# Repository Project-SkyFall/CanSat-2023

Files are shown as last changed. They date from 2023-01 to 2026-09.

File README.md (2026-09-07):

# Disclaimer
This README isn't finished and will be edited in near future

# CanSat-2023
This is a repository of the Czech CanSat team Project SkyFall, winner of CanSat's 2023 Czech national round

<div align="center">
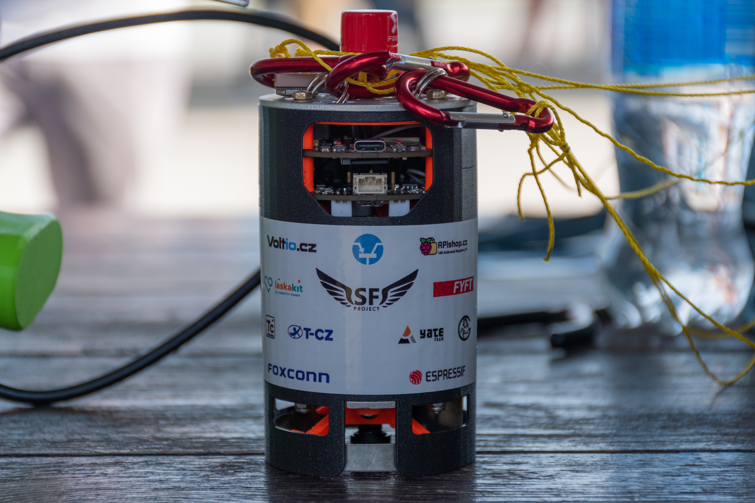
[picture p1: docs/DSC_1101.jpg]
CanSat 2023
  
</div>

## Documentation

<!-- About team -->

## About the team

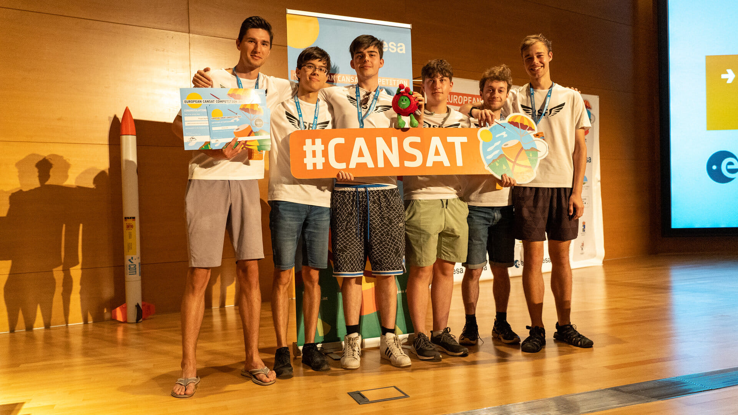
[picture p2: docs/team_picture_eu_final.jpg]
  

  ### Vít Brázda
  <table><tr>
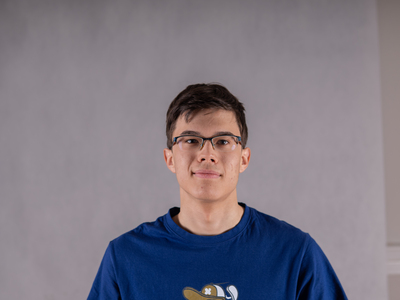
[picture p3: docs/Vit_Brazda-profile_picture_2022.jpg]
    <td width="250"></td>
    <td>Vít is responsible for data visualization running on ground station, as well as making index of habitability of planet, where CanSat is landing. He has a lot of experience regarding Python.</td>
  </tr></table>

  ### David Haisman
  <table><tr>
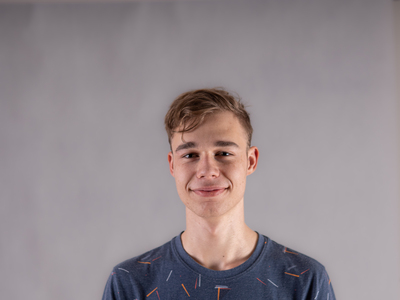
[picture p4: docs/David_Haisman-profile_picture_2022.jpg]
David Haisman
    <td width="250"></td>
    <td>David handles electronics and programming on our CanSat. He designed PCB's, made some libraries and wrote the whole CanSat code. During the development of the CanSat he gained a lot of experience regarding PCB design and programming in C++.</td>
  </tr></table>

  ### Radim Leština
  <table><tr>
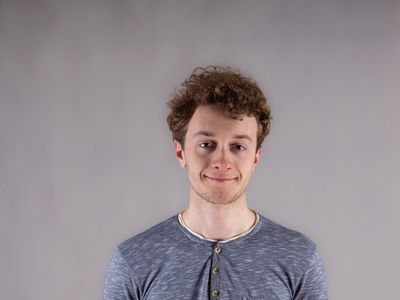
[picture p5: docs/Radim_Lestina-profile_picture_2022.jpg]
Radim Leština
    <td width="250"></td>
    <td>Radim is in charge of designing the outer construction of the CanSat itself. He has a lot of experience in designing and 3D printing mechanical contraptions.</td>
  </tr></table>

  ### Václav Horáček
  <table><tr>
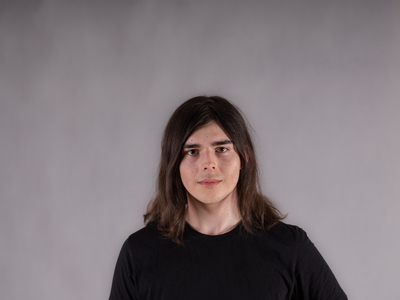
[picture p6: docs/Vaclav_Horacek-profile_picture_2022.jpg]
Václav Horáček
    <td width="250"></td>
    <td>Václav is in charge of multiple departments, mainly the ones for documentation and recovery. In documentation he made the styles, graphics and oversees the documentation making process. His contribution in the recovery department is designing and sewing the CanSat's parachute.</td>
  </tr></table>

  ### Lukáš Nastoupil
  <table><tr>
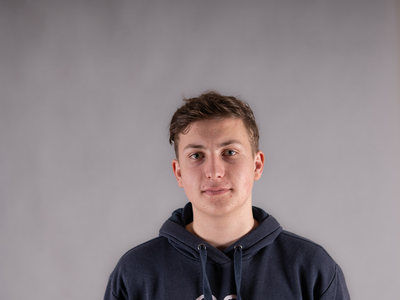
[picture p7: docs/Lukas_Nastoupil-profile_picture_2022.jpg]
Lukáš Nastoupil
    <td width="250"></td>
    <td>Lukáš designed and made the ground station, which is an essential part for our secondary mission. He designed the PCB's, modeled and programmed the ground station. He also worked on the real-time transmission of video from CanSat down to the ground station.</td>
  </tr></table>

  ### Adam Keřka
  <table><tr>
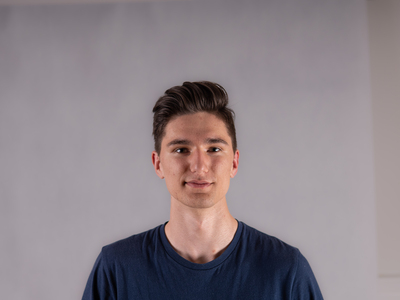
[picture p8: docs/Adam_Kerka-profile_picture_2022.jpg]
Adam Keřka
    <td width="250"></td>
    <td>Adam leads the team itself and also the department of publicity. This mainly includes maintaining social networks accounts and communicating with sponsors. He also designed a lot of the graphics used in advertising and posts on social networks.</td>
  </tr></table>

  ### Vladimír Kašpar
  Ing. Vladimír Kašpar is our mentor in the CanSat competition. We chose Vladimír Kašpar as our mentor based on his experience. In the CanSat 2019 he was a mentor of team Charles the fourth that made it to the European finale. He is also an electronics teacher at SPŠE a VOŠ Pardubice.

  ### Jan Novotný
  Jan Novotný is a freelance developer who makes web and mobile applications. He programmed the Project SkyFall webpage and supports our team on various other competitions and outgoings.

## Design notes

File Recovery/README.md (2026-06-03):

# Recovery

Mission is rather simple: To protect the satellite from hitting the ground at very high speed. <br>
While a primitive solution, a parachute is good enough. <br>
With some calculations, one can determine exact falling speed of the satellite. <br>
<br>
This branch is dedicated to research and realisation of said recovery systems. <br>

## Let's do this...

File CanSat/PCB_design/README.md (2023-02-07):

# PCB design
## Content
* ### [Disclaimer](#disclaimer-1)
* ### [Power Unit](#power-unit-1)

## Disclaimer
PCBs designed in KiCad

## Power Unit
### Description
Power Unit is base PCB from stackup. It charges batteries or supplies rest of CanSat with 5 V power.
### Used ICs
#### MP2639A
* Balances 2s Li-po batteries and charges them from USB
* Overvoltage, overcurrent and overtemperature battery protection
* Step-down battery voltage to 5 V

## Control Unit
### Description

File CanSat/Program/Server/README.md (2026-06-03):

# Pokyny pro ovládání senzorů

- Funkce get_sensors po dotazu na /sensors očekává odpověď ve formátu
```json
[
    {
        "sensor": "<sensor_name>",
        "value": "<sensor_value>"
    }
]
```
Senzory, které chceme pouze zapnout a vypnout, musí mít nastavenou hodnotu `sensor_value` na "on", nebo "off"

- Po volbě stavu senzoru je odeslán dotaz na / s parametry ve tvaru
```json
{
    "sensor": "<sensor_name>",
    "value": "<sensor_value>"
}
```

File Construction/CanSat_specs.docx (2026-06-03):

CanSat

Rozměry

- 115 mm (výška)
- 66 mm (průměr)

Vše musí být uvnitř, vyjma padáku, ten může přidávat velikost pouze směrem nahoru, ne do strany! (stejně jako externí antény), pro externí prvky je nad CanSatem rezervováno 4,5 cm místa.

Váha

300-350 g

Baterie

- Baterie musí být vyjímatelná
- CanSat musí v zapnutém stavu vydržet na baterii minimálně 4 hod. (čistého času)

Padák

- Musí vydržet tažnou sílu 1000 N
- Doporučená přistávací rychlost je 6 m×s⁻¹, nebo míň
- CanSat jako takový musí zvládnout zrychlení 20 g

Budget

Musíme se vejít do 12 729,07 Kč (XD)

Kvalita vzduchu

6,3 x 6,2 x 0,2 cm

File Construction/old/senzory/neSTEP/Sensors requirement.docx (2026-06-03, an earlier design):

Sensor requirements EN

SCD30

- CO2, Humidity, temperature
- Requires acces to „fresh“ air
- Must be out of main air flow and any hot source

SEN0322

- Oxygen
- must not be subject to excessive impact or vibration

BME280

- Humidity
- Just needs „fresh“ air

SD CARD READER

- Data transfer
- Requires easy acces

BATTERIES

- Power supply
- Must be possible to replace it

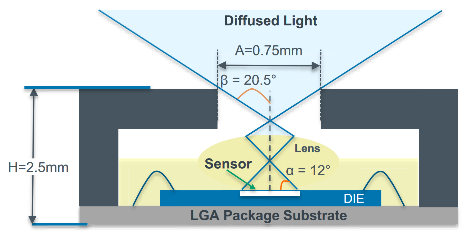
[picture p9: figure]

AS7265X

- Spektrometre
- Needs acces to a ambient light

BH1750

- Light intrnsity
- Needs acces to a ambient light

MPU9250

- Gyroscope, Accelerometer, Magnetometer

Požadavky sensorů CZ

SCD30

- CO2, vlhkost, teplota
- Potřebuje přístup k okolnímu vzduchu
- Musí být mimo hlavní tok vzduchu a jakémukoliv zdroji významného tepla

SEN0322

- Vzduch
- Neměl by být vystaven vibracím, nebo prudkým nárazům (r.i.p.)

BME280

- Vlhkost
- Přístup k okolnímu vzduchu

ČTEČKA SD KARTY

- Přenos dat
- Potřebuje snadný přístup

BATERIE

- Zdroj
- Musí být možné je vyměnit

AS7265X

- Spektrometr
- Potřebuje přístup k okolnímu světlu

BH1750

- Light intrnsity
- Potřebuje přístup k okolnímu světlu

BH1750

- Gyroskop, Akcelerometr, Magnetometr
- Needs acces to a ambient light 8

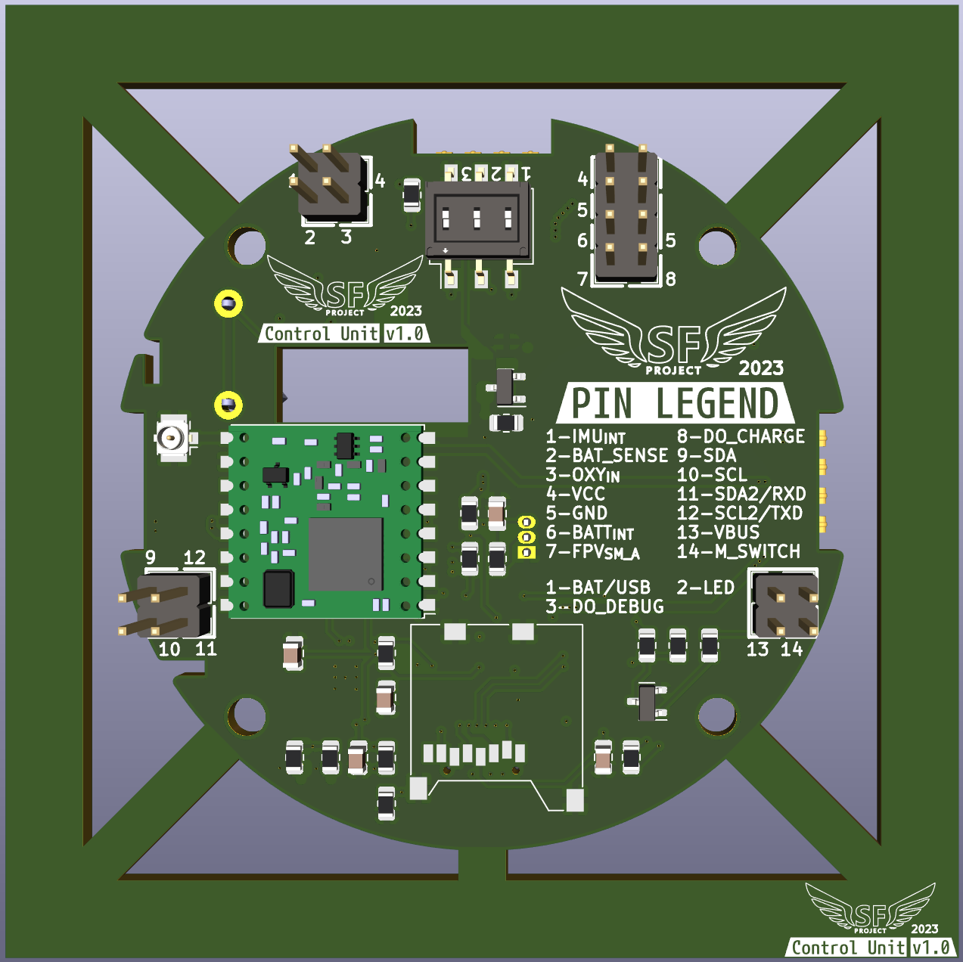
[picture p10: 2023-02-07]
CanSat/PCB_design/Other/Image_Export/Control_Unit_back_v1.0.png

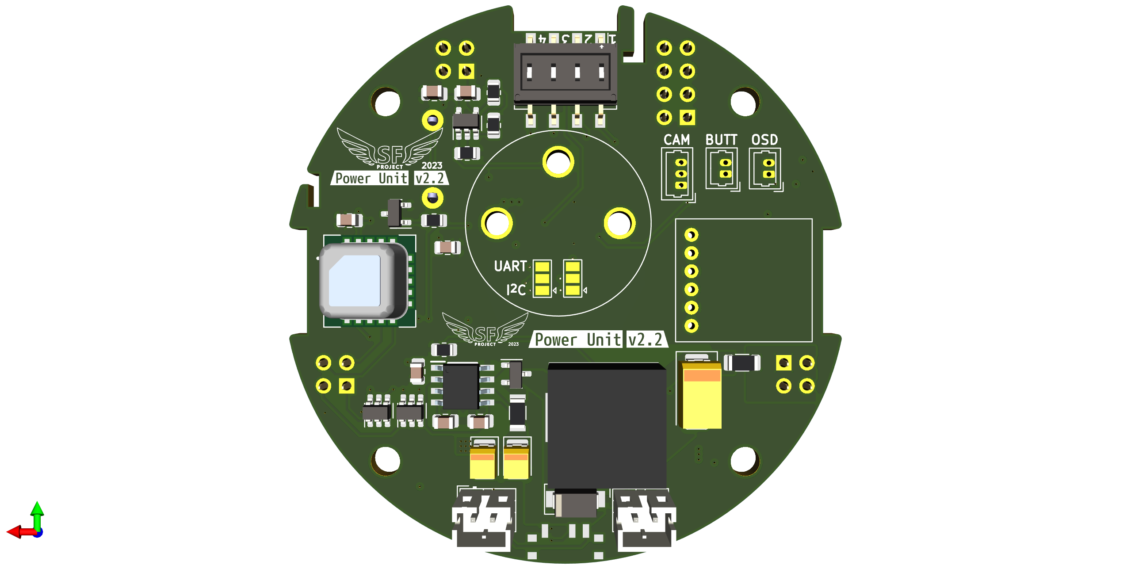
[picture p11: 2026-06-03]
CanSat/PCB_design/Other/Image_Export/Power_Unit_back_v2.2.png

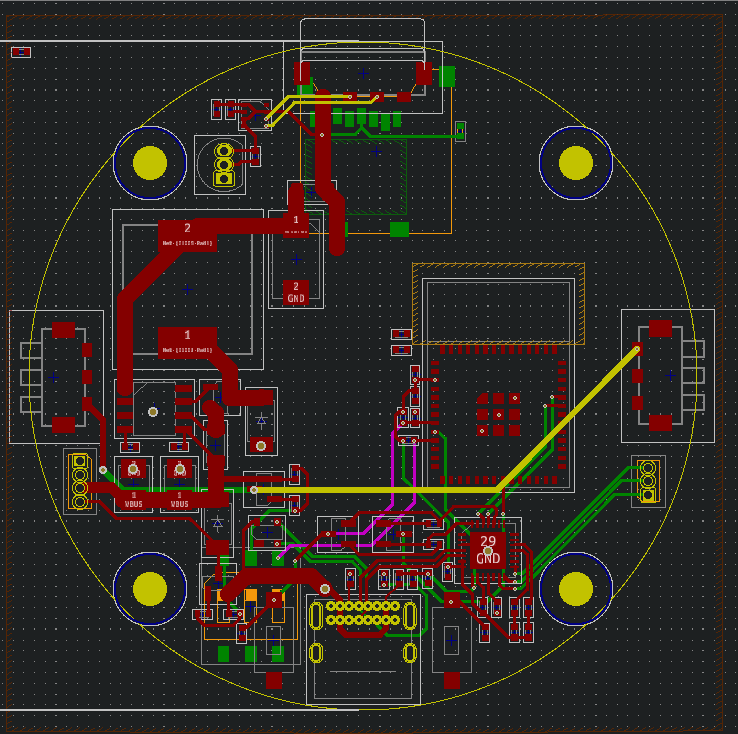
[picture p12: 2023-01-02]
CanSat/PCB_design/Other/T-CZ/Project_SkyFall_Control_Unit.png

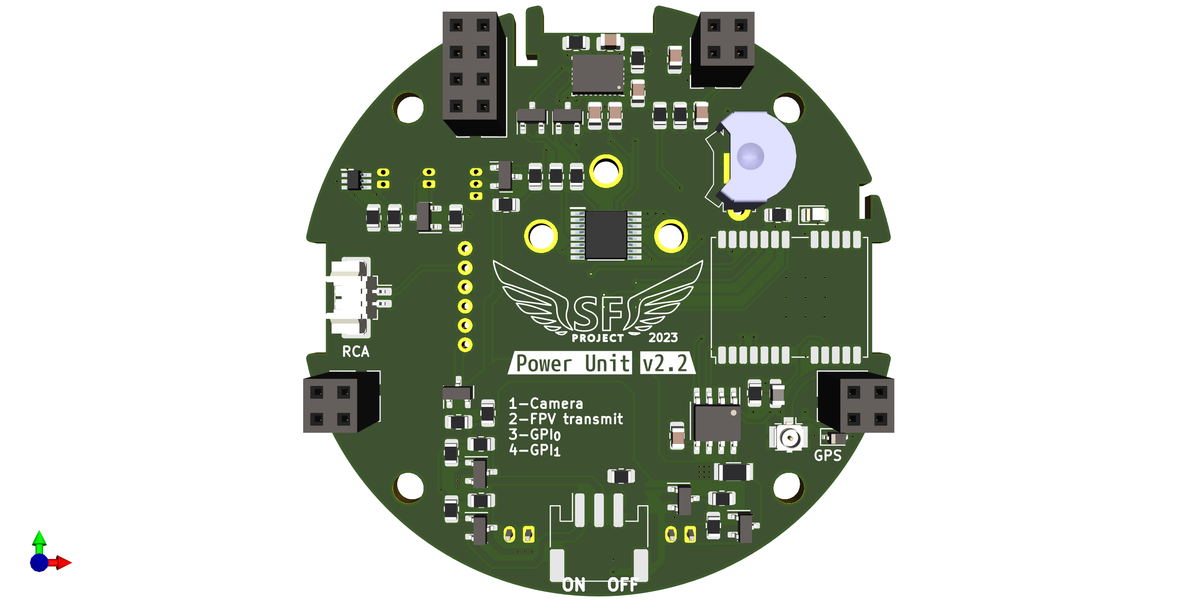
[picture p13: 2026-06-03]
CanSat/PCB_design/Other/Image_Export/Power_Unit_front_v2.2.png

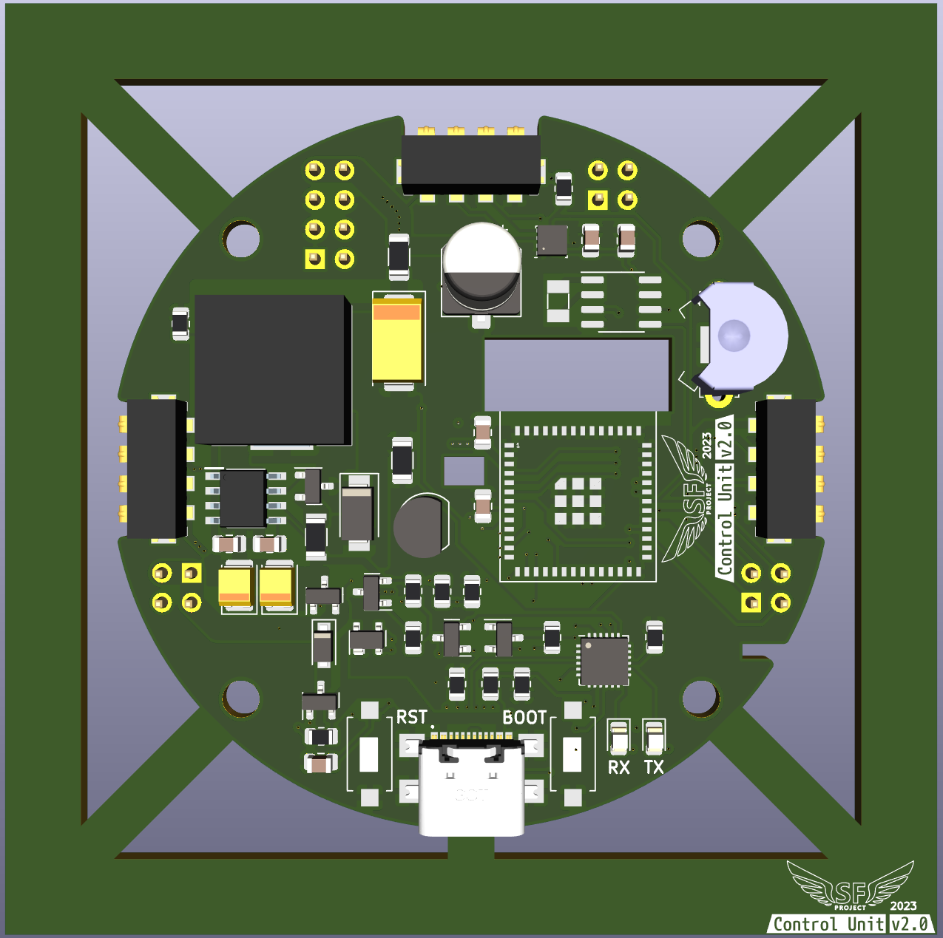
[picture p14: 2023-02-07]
CanSat/PCB_design/Other/Image_Export/Control_Unit_front_v2.0.png

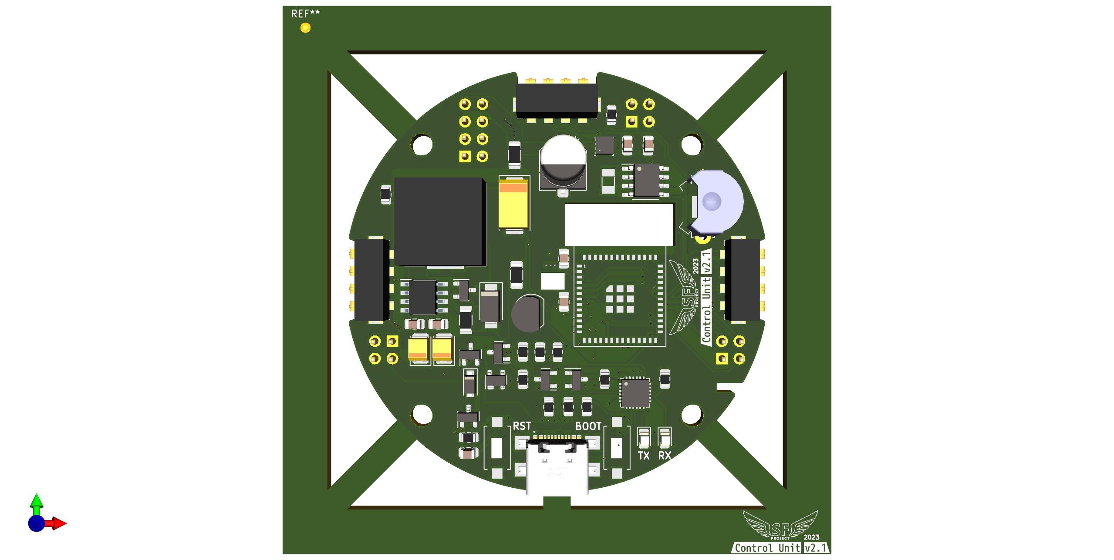
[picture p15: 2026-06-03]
CanSat/PCB_design/Other/Image_Export/Control_Unit_front_v2.1.png

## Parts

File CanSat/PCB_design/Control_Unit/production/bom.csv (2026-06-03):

Designator | Footprint | Quantity | Value | LCSC Part #
AE401 | U.FL_Hirose_U.FL-R-SMT-1_Vertical | 1 | Antenna_Shield
BT701 | 2989 | 1 | Backup battery
C201, C206 | C_0805_2012Metric | 2 | 10uF
C202, C208 | C_0805_2012Metric | 2 | 1uF
C203 | CP_Elec_6.3x7.7 | 1 | 680uF
C204, C205, C207, C301, C302, C303, C504, C601 | C_0805_2012Metric | 8 | 0.1uF
C501, C502 | CP_EIA-3528-21_Kemet-B | 2 | TPSB686K010R0600
C503 | C_0805_2012Metric | 1 | 0.47uF
C505 | CP_EIA-7343-31_Kemet-D | 1 | 293D227X9010D2TE3
D201 | D_SOD-123F | 1 | SBR3U40S1F-7
D202, D203 | LED_0805_2012Metric | 2 | APT2012LSECK/J4-PRV
D204 | SOT-143 | 1 | SP0503BAHT
D501 | D_SMA | 1 | B330A
J101 | PinHeader_2x04_P2.54mm_Vertical | 1 | Conn_02x04_Male
J102, J103, J104 | PinHeader_2x02_P2.54mm_Vertical | 3 | Conn_02x02_Male
J105, J106, J107 | 009155004541006 | 3 | 009155004541006
J201 | USB4110GFA | 1 | USB4110-GF-A
J601 | DS1139-05 | 1 | Micro_SD_Card 823-046
L501 | CDRH125101MC | 1 | CDRH125NP-220MC
Q201, Q203, Q207, Q501 | SOT-23 | 4 | SI2305CDS-T1-BE3
Q202, Q204, Q205, Q206 | SOT-23 | 4 | BC847
R201 | R_0805_2012Metric | 1 | 1k
R202 | R_0805_2012Metric | 1 | 22k1
R203, R209, R214, R221 | R_0805_2012Metric | 4 | 100k
R204, R205, R206, R210, R211, R223, R224, R226 | R_0805_2012Metric | 8 | 10k
R207 | R_0805_2012Metric | 1 | 47k5
R208 | R_0805_2012Metric | 1 | 27k
R212 | R_0805_2012Metric | 1 | 47k
R213, R502 | R_1206_3216Metric | 2 | 0R
R215, R216 | R_0805_2012Metric | 2 | 750R
R217, R218, R219 | R_0805_2012Metric | 3 | 5k1
R220, R222, R225 | R_0805_2012Metric | 3 | 5k
R301 | R_0805_2012Metric | 1 | 4k7
R501 | R_1206_Current | 1 | PE1206FRE470R04L
SW201 | SW_DIP_SPSTx03_Slide_Omron_A6S-310x_W8.9mm_P2.54mm | 1 | DS04-254-1-03BK-SMT
SW202, SW203 | Tlačítko SMD LaskaKit | 2 | LaskaKit tlačítko
U201 | QFN-24-1EP_4x4mm_P0.5mm_EP2.6x2.6mm | 1 | CP2102N-Axx-xQFN24
U202 | ESP32-MINI-1 | 1 | ESP32-MINI-1
U301 | TO-92_Inline | 1 | DS18B20
U302 | Bosch_LGA-8_2.5x2.5mm_P0.65mm_ClockwisePinNumbering | 1 | BME280
U401 | HOPERF_RFM9XW_SMD | 1 | RFM96W-433S2
U501 | SOIC127P600X175-8N | 1 | MAX1626ESA+T
U701 | SOIC-8-1EP_3.9x4.9mm_P1.27mm_EP2.29x3mm | 1 | PT7C4339
Y701 | ECX-31B | 1 | ECS-.327-6-34B-C-TR

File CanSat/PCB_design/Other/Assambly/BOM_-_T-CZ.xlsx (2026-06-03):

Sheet: Power Unit
Id | Designator | Package | Quantity | Designation | Supplier and ref | Column1
28 | AE1001 | U.FL_Hirose_U.FL-R-SMT-1_Vertical | 1 | Antenna_Shield
26 | BT1001 | 2989 | 1 | Backup battery
45 | BT301,BT302 | JST_PH_B2B-PH-K_1x02_P2.00mm_Vertical | 2 | Battery_Cell
44 | C1103 | C_0805_2012Metric | 1 | 10nF
8 | C1202,C1102,C401 | C_0805_2012Metric | 3 | 10uF
3 | C1204,C702,C302,C1203,C707,C706,C301 | C_0805_2012Metric | 7 | 22uF
13 | C701,C704,C1002,C803,C804,C1101,C901 | C_0805_2012Metric | 7 | 0.1uF
40 | C703 | C_0805_2012Metric | 1 | 4.7uF
32 | C705,C1001,C708 | C_0805_2012Metric | 3 | 1uF
59 | C801 | C_0805_2012Metric | 1 | 120nF
50 | C802 | C_0805_2012Metric | 1 | 6.8nF
39 | D1001 | LED_0805_2012Metric | 1 | APT2012LSECK/J4-PRV
42 | D701 | D_SMA | 1 | B330A
12 | D702,D705,D703,D704 | LED_0805_2012Metric | 4 | APT2012LZGCK
24 | D706 | LED_0805_2012Metric | 1 | APT2012LSECK/J3-PRV
25 | J101 | PinSocket_2x04_P2.54mm_Vertical | 1 | Conn_02x04_Female
2 | J102,J103,J104 | PinSocket_2x02_P2.54mm_Vertical | 3 | Conn_02x02_Female
18 | J501 | Molex_PicoBlade_53261-0271_1x02-1MP_P1.25mm_Horizontal | 1 | Conn_01x02
63 | J502 | Molex_PicoBlade_53047-0310_1x03_P1.25mm_Vertical | 1 | Conn_01x03
55 | J504,J503 | Molex_PicoBlade_53047-0210_1x02_P1.25mm_Vertical | 2 | Conn_01x02
29 | L1001 | L_0805_2012Metric | 1 | 27nH
20 | L701 | L_Bourns_SRP7050AA | 1 | SRP7050AA-2R2M
17 | Q1205,Q208,Q1201,Q1204,Q1202 | SOT-23 | 5 | BC857
9 | Q206,Q301,Q201,Q501,Q209,Q210,Q202,Q204,Q205,Q302,Q1203,Q1206,Q1001,Q203 | SOT-23 | 14 | BC847
22 | Q212,Q211,Q207 | SOT-23 | 3 | SI2305CDS-T1-BE3
19 | R1001 | R_0805_2012Metric | 1 | 12R
15 | R1003,R713 | R_0805_2012Metric | 2 | 750R
46 | R1004,R1002 | Cu_Conn-R_0805_2012Metric | 2 | CU_CONN-R_0805_2012Metric |  | Pouze 0R 0805 rezistory - v PDF je vyznačeno, ve které pozici mají být osazené
57 | R1102 | R_0805_2012Metric | 1 | 20k
53 | R1103,R1101 | R_0805_2012Metric | 2 | 100R
61 | R1203 | R_0805_2012Metric | 1 | 15k
4 | R1205,R213,R215,R212,R217,R219,R221,R1209,R1202,R1204,R1206,R1207,R207,R1208 | R_0805_2012Metric | 14 | 100k
52 | R210 | R_1206_3216Metric | 1 | 0R
1 | R214,R203,R501,R204,R206,R1005 | R_0805_2012Metric | 6 | 5k
49 | R216 | R_0805_2012Metric | 1 | 12k
47 | R218 | R_0805_2012Metric | 1 | 5k1
35 | R303,R302 | R_0805_2012Metric | 2 | 220k
5 | R304,R222,R205,R711,R201,R701,R211,R202,R705,R220,R209,R801,R301,R802,R1201,R208 | R_0805_2012Metric | 16 | 10k
43 | R401 | R_1206_Current | 1 | PE1206FRE470R04L
41 | R702 | R_0805_2012Metric | 1 | 82k
34 | R703 | R_0805_2012Metric | 1 | 820k
11 | R704 | R_0805_2012Metric | 1 | 3k16
31 | R706 | R_0805_2012Metric | 1 | 27k4
36 | R707 | R_0805_2012Metric | 1 | 1k87
10 | R708 | R_0805_2012Metric | 1 | 5k11
30 | R709 | R_0805_2012Metric | 1 | 143k
37 | R710 | R_0805_2012Metric | 1 | 75k
7 | R714,R716,R712,R715 | R_0805_2012Metric | 4 | 330R
38 | R717 | R_0805_2012Metric | 1 | 0R5
16 | SW201 | SW_DIP_SPSTx04_Slide_Omron_A6S-410x_W8.9mm_P2.54mm | 1 | DS04-254-1-04BK-SMT
62 | SW202 | PCM12SMTR | 1 | PCM12SMTR
6 | SW203 | Tlačítko SMD LaskaKit | 1 | LaskaKit tlačítko
48 | TH301,TH302 | Molex_PicoBlade_53047-0210_1x02_P1.25mm_Vertical | 2 | NRBE104J3435B2J |  | Pouze Molex_Picoblade konektor
23 | U1001 | ublox_NEO | 1 | NEO-M9N
54 | U1101 | SOT-23-5 | 1 | MCP6486UT-E/OT
58 | U1102 | ME2-O2 | 1 | ME2-02
33 | U201 | SO-16_5.3x10.2mm_P1.27mm | 1 | PCA8574D
64 | U401 | SOIC-8_3.9x4.9mm_P1.27mm | 1 | INA219AxD
21 | U501 | SOT65P210X110-6N | 1 | AD5246BKSZ100
56 | U601 | TBS UNIFY PRO32 5G8 nano | 1 | TBS_UNIFY_PRO32_5G8_nano
27 | U702 | MP2639AGRZ | 1 | MP2639AGR-Z
14 | U703,U301,U701 | SOT-23-6 | 3 | TS5A3159DBV
60 | U801 | LGA-28_5.2x3.8mm_P0.5mm | 1 | BNO055
51 | U901 | XDCR_SCD41-D-R2 | 1 | SCD41

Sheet: Control Unit
Id | Designator | Package | Quantity | Designation | Supplier and ref | Column1
41 | AE401 | U.FL_Hirose_U.FL-R-SMT-1_Vertical | 1 | Antenna_Shield
14 | BT701 | 2989 | 1 | Backup battery
18 | C203 | CP_Elec_6.3x7.7 | 1 | 680uF
32 | C206,C201 | C_0805_2012Metric | 2 | 10uF
11 | C208,C202 | C_0805_2012Metric | 2 | 1uF
4 | C302,C205,C504,C301,C601,C204,C207,C303 | C_0805_2012Metric | 8 | 0.1uF
22 | C502,C501 | CP_EIA-3528-21_Kemet-B | 2 | TPSB686K010R0600
17 | C503 | C_0805_2012Metric | 1 | 0.47uF
27 | C505 | CP_EIA-7343-31_Kemet-D | 1 | 293D227X9010D2TE3
29 | D201 | D_SOD-123F | 1 | SBR3U40S1F-7
24 | D202,D203 | LED_0805_2012Metric | 2 | APT2012LSECK/J4-PRV
12 | D204 | SOT-143 | 1 | SP0503BAHT
7 | D501 | D_SMA | 1 | B330A
42 | J101 | PinHeader_2x04_P2.54mm_Vertical | 1 | Conn_02x04_Male
36 | J104,J103,J102 | PinHeader_2x02_P2.54mm_Vertical | 3 | Conn_02x02_Male
8 | J105,J106,J107 | 009155004541006 | 3 | 009155004541006
30 | J201 | USB4110GFA | 1 | USB4110-GF-A
44 | J601 | DS1139-05 | 1 | Micro_SD_Card 823-046
26 | L501 | CDRH125101MC | 1 | CDRH125NP-220MC
2 | Q201,Q203,Q501,Q207 | SOT-23 | 4 | SI2305CDS-T1-BE3
21 | Q205,Q206,Q204,Q202 | SOT-23 | 4 | BC847
37 | R201 | R_0805_2012Metric | 1 | 1k
15 | R202 | R_0805_2012Metric | 1 | 22k1
6 | R207 | R_0805_2012Metric | 1 | 47k5
34 | R208 | R_0805_2012Metric | 1 | 27k
23 | R209,R221,R203,R214 | R_0805_2012Metric | 4 | 100k
20 | R211,R204,R223,R206,R226,R224,R205,R210 | R_0805_2012Metric | 8 | 10k
10 | R212 | R_0805_2012Metric | 1 | 47k
3 | R213,R502 | R_1206_3216Metric | 2 | 0R
39 | R216,R215 | R_0805_2012Metric | 2 | 750R
16 | R217,R219,R218 | R_0805_2012Metric | 3 | 5k1
19 | R225,R220,R222 | R_0805_2012Metric | 3 | 5k
38 | R301 | R_0805_2012Metric | 1 | 4k7
35 | R501 | R_1206_Current | 1 | PE1206FRE470R04L
40 | SW201 | SW_DIP_SPSTx03_Slide_Omron_A6S-310x_W8.9mm_P2.54mm | 1 | DS04-254-1-03BK-SMT
13 | SW203,SW202 | Tlačítko SMD LaskaKit | 2 | LaskaKit tlačítko
9 | U201 | QFN-24-1EP_4x4mm_P0.5mm_EP2.6x2.6mm | 1 | CP2102N-Axx-xQFN24
28 | U202 | ESP32-MINI-1 | 1 | ESP32-MINI-1
1 | U301 | TO-92_Inline | 1 | DS18B20
33 | U302 | Bosch_LGA-8_2.5x2.5mm_P0.65mm_ClockwisePinNumbering | 1 | BME280
43 | U401 | HOPERF_RFM9XW_SMD | 1 | RFM96W-433S2
5 | U501 | SOIC127P600X175-8N | 1 | MAX1626ESA+T
31 | U701 | SOIC-8-1EP_3.9x4.9mm_P1.27mm_EP2.29x3mm | 1 | PT7C4339
25 | Y701 | ECX-31B | 1 | ECS-.327-6-34B-C-TR

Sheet: Side Unit
Id | Designator | Package | Quantity | Designation | Supplier and ref | Column1 | _1
1 | C402,C505,C507,C506,C602,C504,C608,C603,C606,C301,C305,C604,C501,C503,C401,C607,C601,C508,C303,C605,C502 | C_0805_2012Metric | 21 | 0.1uF
2 | C306,C302,C304,C307 | C_0805_2012Metric | 4 | 1uF
3 | U302 | AMS_LGA-20_4.7x4.5mm_P0.65mm | 1 | AS72652
4 | D606,D504,D508,D502,D506,D608,D507,D603,D501,D602,D503,D604,D601,D505,D607,D605 | LED_WS2812B_PLCC4_5.0x5.0mm_P3.2mm | 16 | WS2812B
5 | U304 | SOIC-8_3.9x4.9mm_P1.27mm | 1 | AT25SF041B-SSHD-B
6 | R301,R202,R302,R305,R304,R306,R201,R303 | R_0805_2012Metric | 8 | 10k
7 | U401 | WSOF6 | 1 | BH1730
8 | U301 | AMS_LGA-20_4.7x4.5mm_P0.65mm | 1 | AS72651
9 | U303 | AMS_LGA-20_4.7x4.5mm_P0.65mm | 1 | AS72653

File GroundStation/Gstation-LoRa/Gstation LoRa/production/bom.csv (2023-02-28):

Designator | Footprint | Quantity | Value | LCSC Part #
AE1 | U.FL_Hirose_U.FL-R-SMT-1_Vertical | 1 | Antenna_Shield
J1 | HOPERF_RFM9XW_SMD | 1 | Conn_02x08_Counter_Clockwise
J2 | PinHeader_1x06_P2.54mm_Vertical | 1 | Conn_01x06_Male
J3 | PinHeader_1x08_P2.54mm_Vertical | 1 | Conn_01x08_Male

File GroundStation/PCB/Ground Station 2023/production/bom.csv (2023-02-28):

Designator | Footprint | Quantity | Value | LCSC Part #
ADC1 | AD | 1 | AD
BME1 | BME280 | 1 | BME280
BT1, BT2 | Battery box | 2 | Battery_Cell
GPS1 | GPS | 1 | GY-NEO6MV2
LORA1 | Lora deska | 1 | LORA
RASPI1 | Raspberry pi 4B | 1 | Raspberry PI 4B
STEPDOWN1 | StepDown | 1 | StepDown
SW1 | JST_XH_B2B-XH-A_1x02_P2.50mm_Vertical | 1 | Přepínač
USB-C1 | JST_XH_B2B-XH-A_1x02_P2.50mm_Vertical | 1 | USB-C

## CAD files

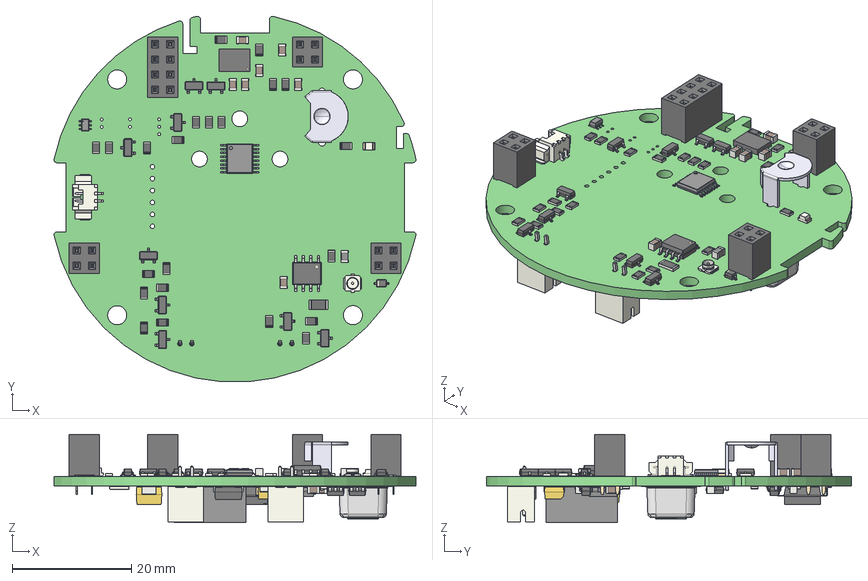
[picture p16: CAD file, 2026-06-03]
CanSat/PCB_design/Other/3D_export/Power_Unit-2.step
60.7 x 61.3 x 14.8 mm
_autosave-Power Unit 2 PCB

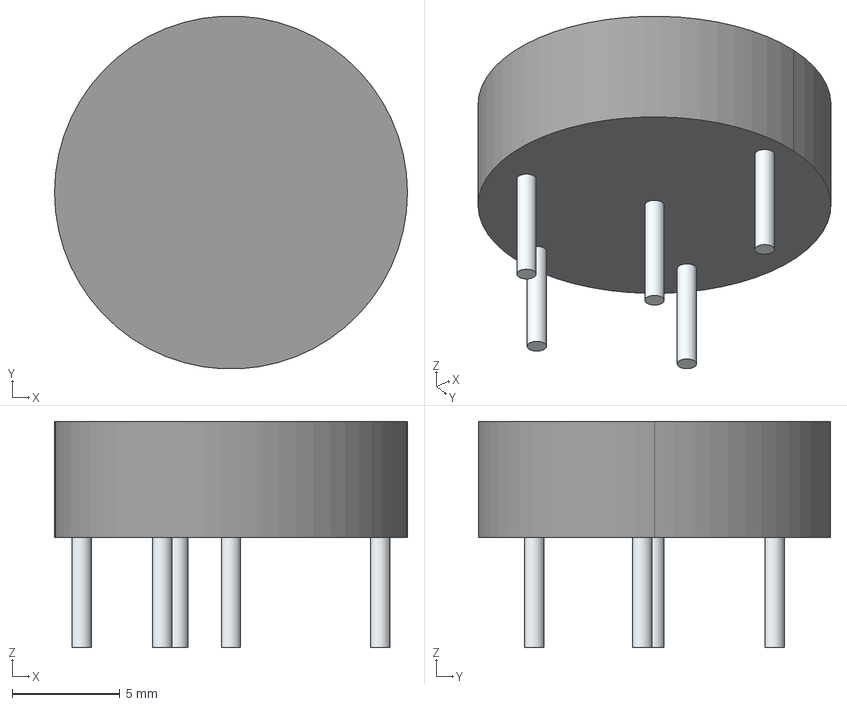
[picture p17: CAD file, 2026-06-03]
CanSat/PCB_design/Other/3D_models/LIB_122-2312-GR/122-2312-GR/3D/122-2312-GR.stp
16.4 x 16.4 x 10.5 mm
Leads x 5

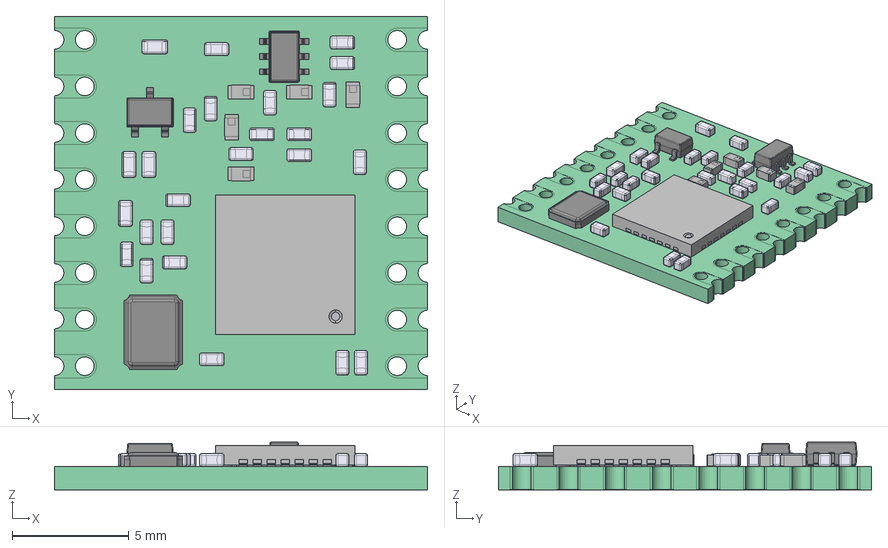
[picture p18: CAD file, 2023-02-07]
CanSat/PCB_design/Other/3D_models/RFM95_LoRa_v15.stp
16.0 x 16.0 x 2.04 mm
QFN 28 v21
QFN 28 v22
QFN 28 v23
QFN 28 v24
QFN 28 v25
QFN 28 v26
QFN 28 v27
QFN 28 v28
QFN 28 v29
QFN 28 v210
QFN 28 v211
QFN 28 v212
QFN 28 v213
QFN 28 v214
QFN 28 v215
QFN 28 v216
QFN 28 v217
QFN 28 v218
QFN 28 v219
QFN 28 v220
QFN 28 v221
QFN 28 v222
QFN 28 v223
QFN 28 v224
QFN 28 v225
QFN 28 v226
QFN 28 v227
QFN 28 v228
QFN 28 v229
QFN 28 v230
QFN 28 v231
QFN 28 v232
QFN 28 v233
QFN 28 v234
QFN 28 v235
QFN 28 v236
QFN 28 v237
QFN 28 v238
QFN 28 v239
QFN 28 v240
QFN 28 v241
QFN 28 v242
QFN 28 v243
QFN 28 v244
QFN 28 v245
QFN 28 v246
QFN 28 v247
QFN 28 v248
QFN 28 v249
QFN 28 v250
QFN 28 v251
QFN 28 v252
QFN 28 v253
QFN 28 v254
QFN 28 v255
QFN 28 v256
QFN 28 v257
QFN 28 v258
SMD Crystal v1
CAP 0403 v1 x 8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

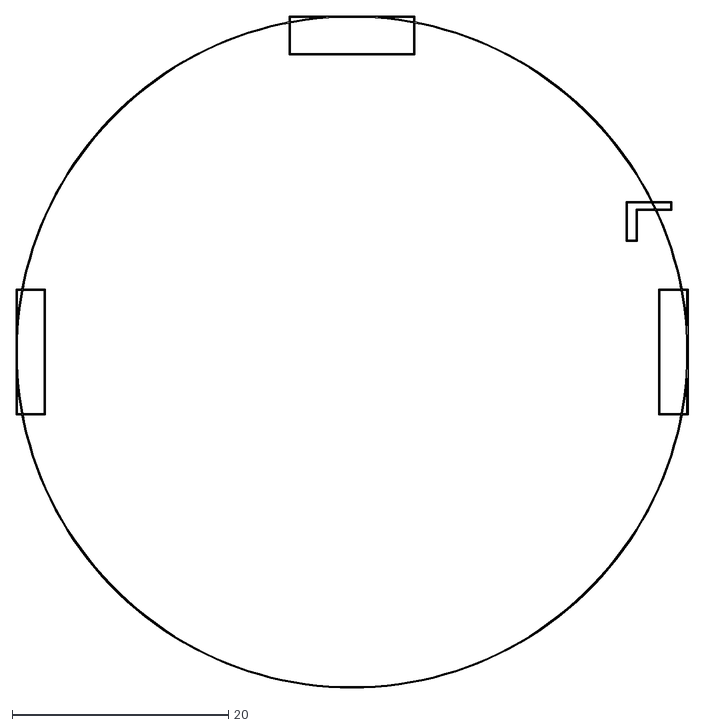
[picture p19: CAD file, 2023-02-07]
CanSat/PCB_design/Other/DXF/Power_Unit-Edge_Cuts.dxf
62.1 x 62.1

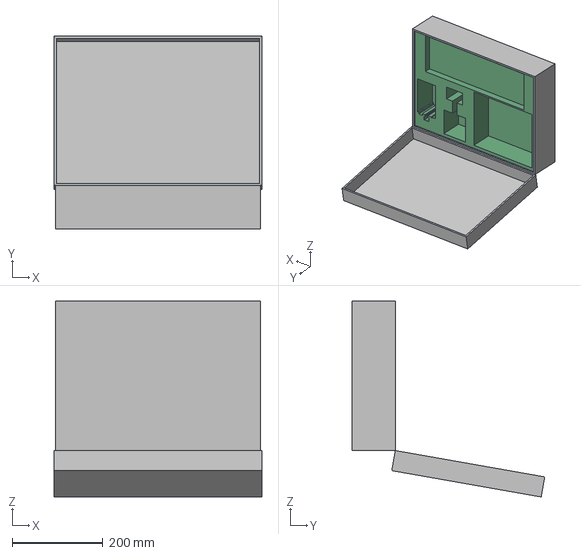
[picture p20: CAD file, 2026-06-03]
Construction/CanSat/Kufr prototyp.stp
459.0 x 424.9 x 432.5 mm

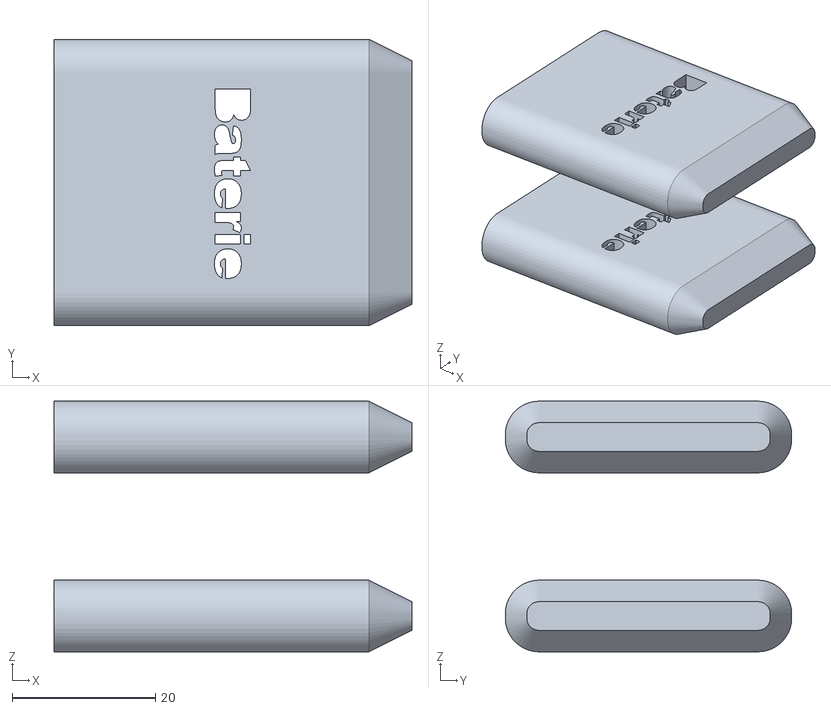
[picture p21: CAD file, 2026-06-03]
Construction/CanSat/test/baterky.stl
50.0 x 40.0 x 35.0

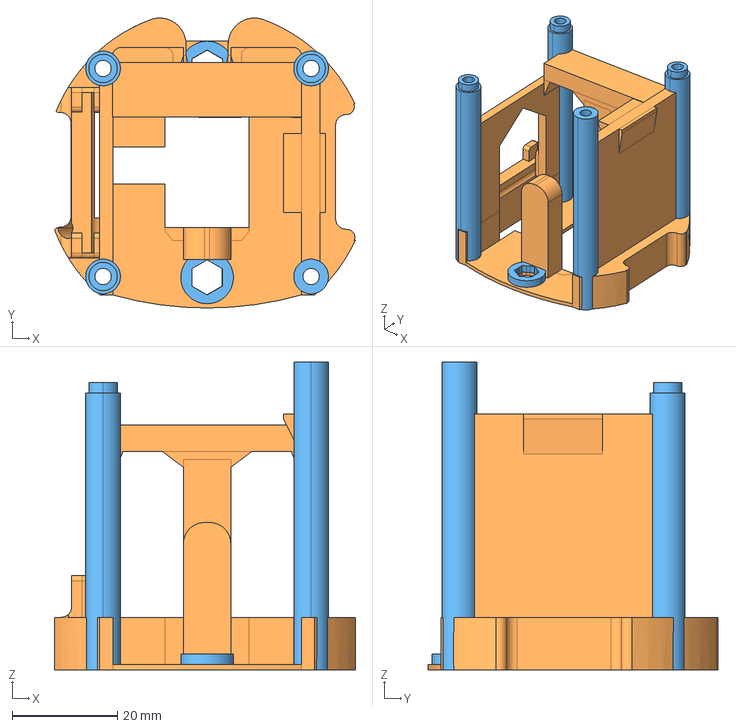
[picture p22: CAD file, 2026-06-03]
Construction/CanSat/tisk/Nový/btdmck.stp
57.2 x 55.1 x 58.5 mm

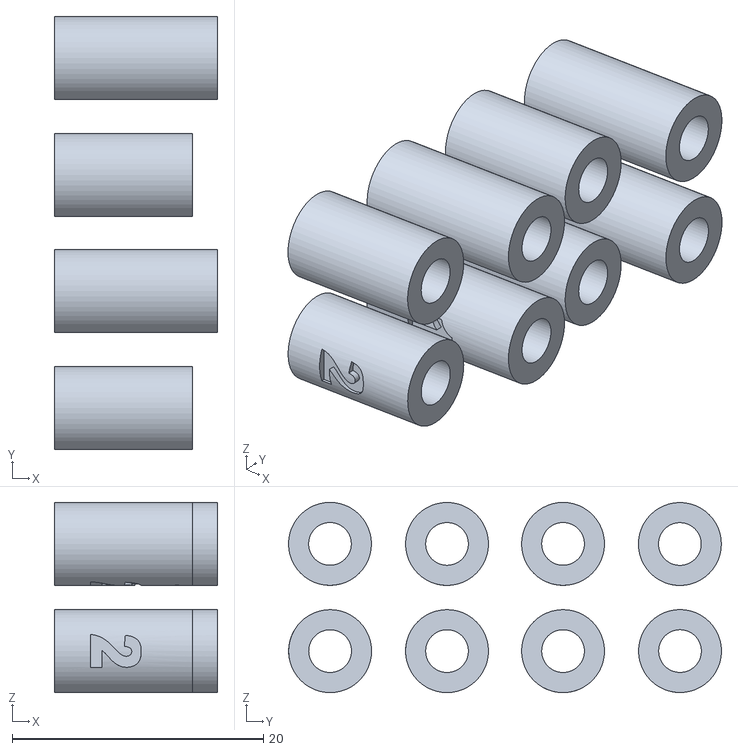
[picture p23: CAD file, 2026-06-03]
Construction/CanSat/tisk/sloupky.stl
13.0 x 34.4 x 15.1

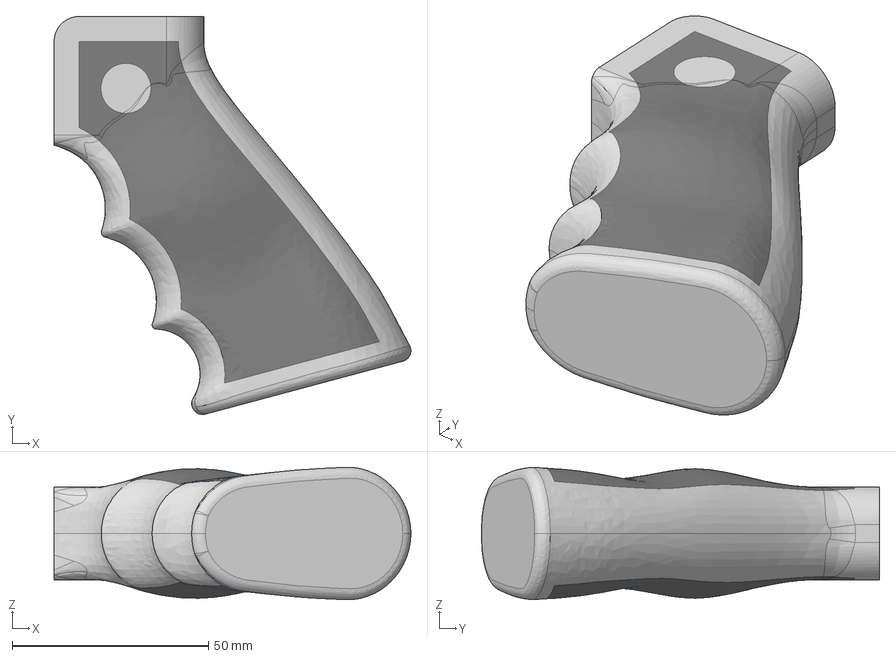
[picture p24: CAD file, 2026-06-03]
Construction/GrounStation/GRIP 2.step
90.8 x 101.3 x 33.7 mm

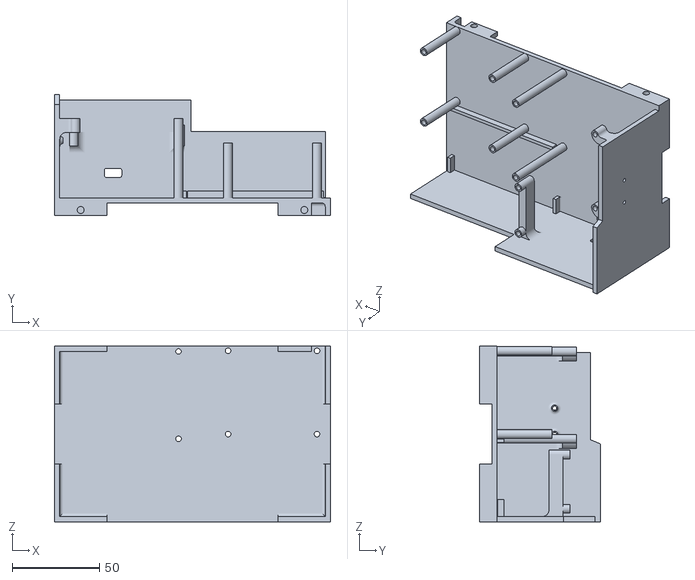
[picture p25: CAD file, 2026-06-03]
Construction/GrounStation/přednáška stl/BOTTOM.stl
158.0 x 69.0 x 100.5

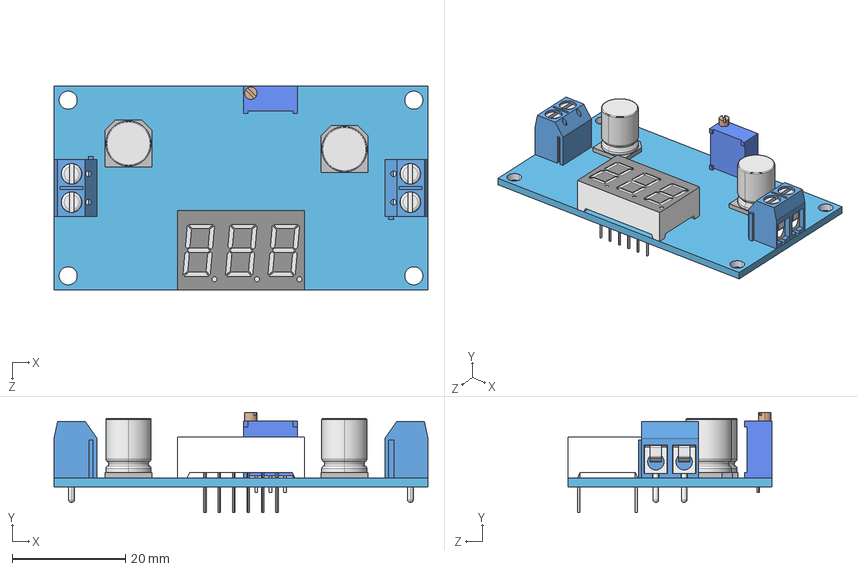
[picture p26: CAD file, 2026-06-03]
Construction/GrounStation/STEP/LM2596 StepDown.STEP
66.0 x 17.6 x 36.0 mm
BASE, LM2596 Buck Converter 4.0-40 to 1.3-37V
DG301-5.0-02, LM2596 Buck Converter 4.0-40 to 1.3-37V x 2
3 DIGIT 7 SEGMENT DISPLAY, LM2596 Buck Converter 4.0-40 to 1.3-37V
Trimpot 3296W, LM2596 Buck Converter 4.0-40 to 1.3-37V_Valor predeterminado
220 35V CAPACITOR, LM2596 Buck Converter 4.0-40 to 1.3-37V x 2

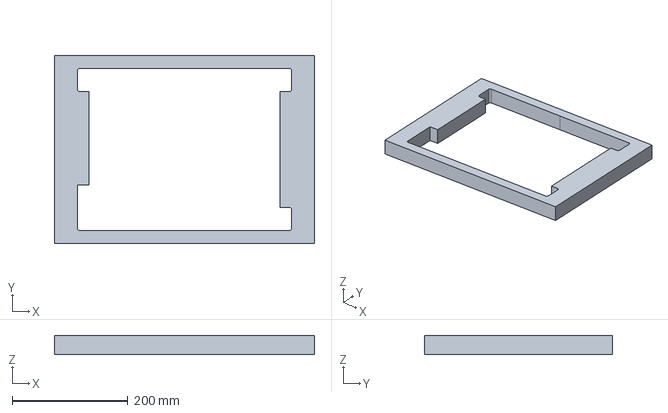
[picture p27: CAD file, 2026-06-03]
Construction/GrounStation/Suitcase filling/pěna-horni1.stp
449.0 x 325.0 x 33.0 mm

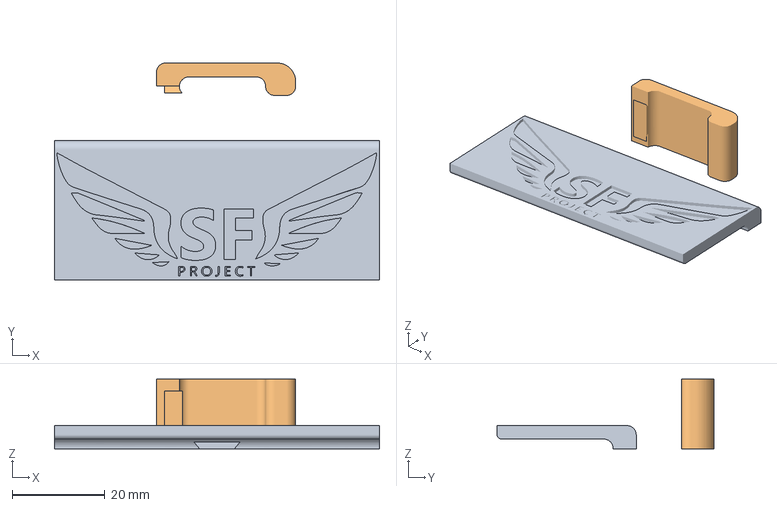
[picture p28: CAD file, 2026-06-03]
Construction/klipsna s logem.3mf
70.0 x 46.7 x 15.0 mm
klipsna s logem.stl x 2

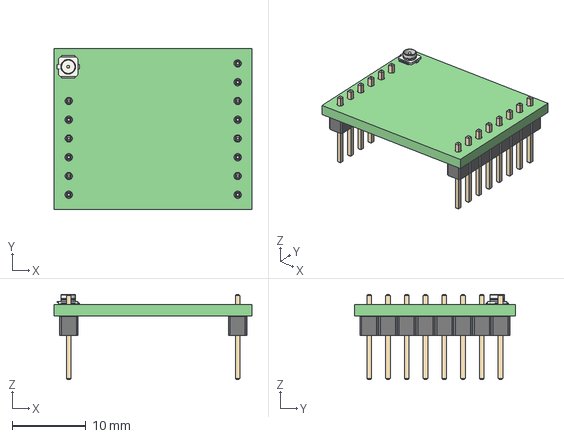
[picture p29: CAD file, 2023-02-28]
GroundStation/Gstation-LoRa/Gstation LoRa/Gstation LoRa.step
26.8 x 21.8 x 11.5 mm
_autosave-Gstation LoRa PCB

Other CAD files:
CanSat/PCB_design/Other/3D_export/Power_Unit.step
CanSat/PCB_design/Other/3D_models/SEN0322_Gravity_Oxygen.stp
CanSat/PCB_design/Other/DXF/Control_Unit-Edge_Cuts_Edited.dxf
Construction/CanSat/Antena TBS Unify Pro 5G8.step
CanSat/PCB_design/Other/3D_export/Side_Unit.step
CanSat/PCB_design/Other/3D_models/LIB_122-2312-GR/122-2312-GR/Allegro/1222312gr.psm
CanSat/PCB_design/Other/3D_models/LIB_122-2312-GR/122-2312-GR/DEHDL/122_2312_gr/chips/chips.prt
CanSat/PCB_design/Other/DXF/62mm_diameter_+_threaded_rod.dxf
CanSat/PCB_design/Other/DXF/Control_Unit-B_Fab.dxf
CanSat/PCB_design/Other/DXF/Control_Unit-Edge_Cuts.dxf
CanSat/PCB_design/Other/DXF/Control_Unit-Edge_Cuts_Edited_threaded.dxf
CanSat/PCB_design/Other/DXF/Logo_vFINAL.dxf
CanSat/PCB_design/Other/DXF/Power_Unit-Edge_Cuts_Edited.dxf
CanSat/PCB_design/Other/DXF/Power_Unit-Edge_Cuts_Edited_threaded.dxf
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

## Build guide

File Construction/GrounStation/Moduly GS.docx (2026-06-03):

CPU

- https://www.laskakit.cz/iot-esp-32s-2-4ghz-dual-mode-wifi-bluetooth-rev-1--cp2102/

LORA

- https://www.laskakit.cz/hoperf-rfm96w-433mhz-komunikacni-modul/#relatedFiles

SD-CARD

- https://www.laskakit.cz/microsd-card-modul-spi/

POWER

- https://www.laskakit.cz/3350mah-panasonic-ncr18650b-18650-li-ion-baterie/
- https://www.laskakit.cz/nabijecka-liitokala-lii-pd4-pro-li-ion--li-fe-a-ni-mh-baterie/

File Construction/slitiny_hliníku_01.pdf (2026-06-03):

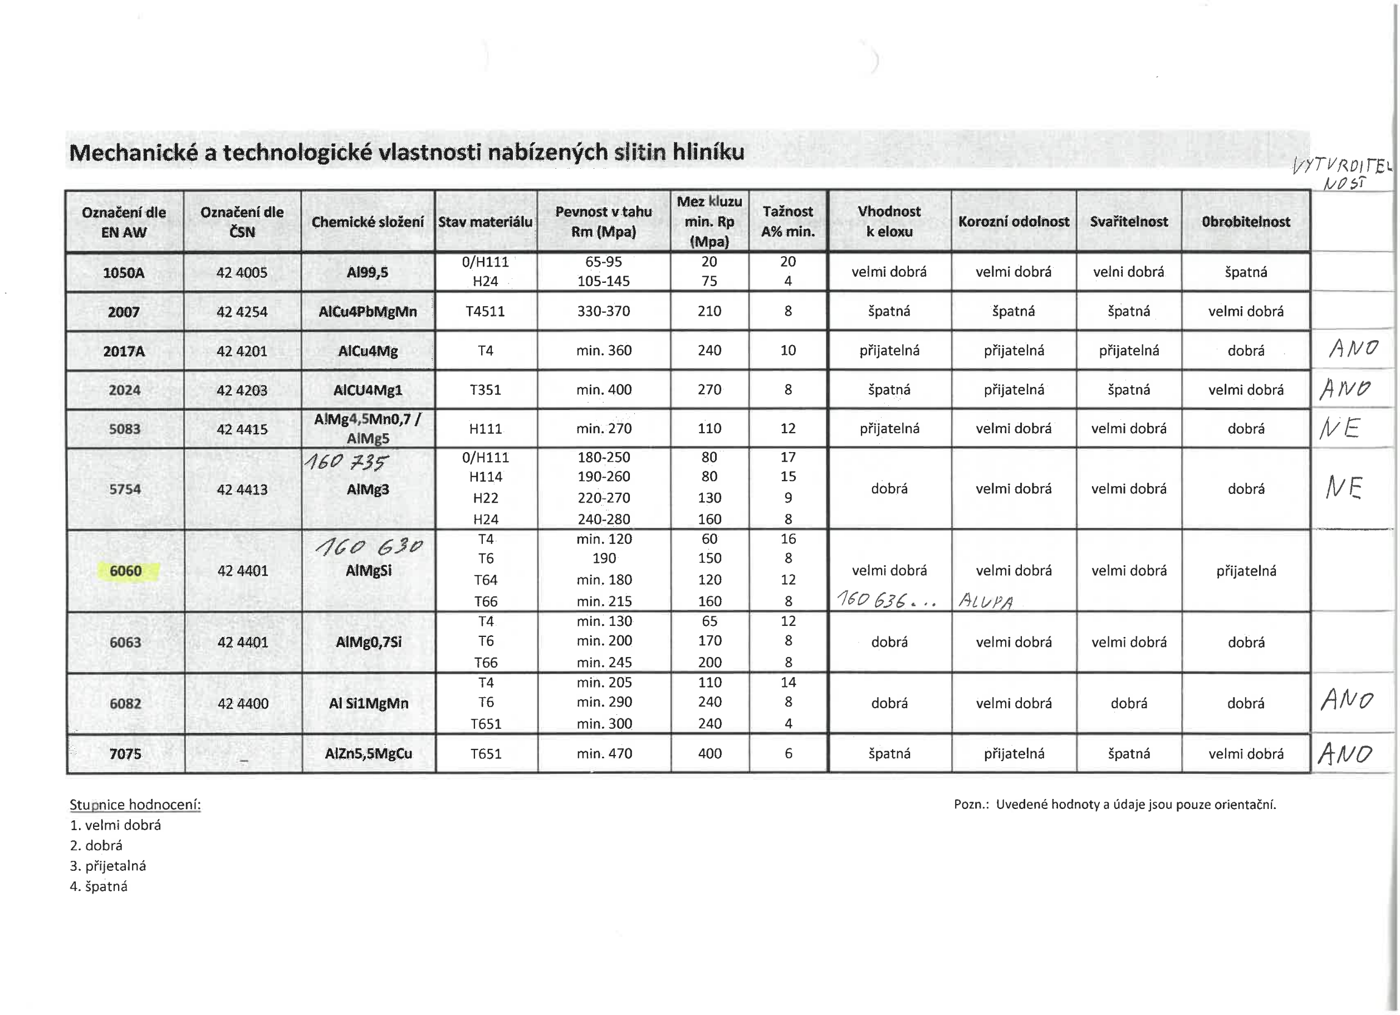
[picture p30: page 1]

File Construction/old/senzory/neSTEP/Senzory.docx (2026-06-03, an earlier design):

CanSat Ground Station

~~BME280~~ ~~LoRa~~

~~MPU9250~~ IoT ESP-WROOM-32

~~GPS~~ micro SD card

~~Baterie~~ Li-Ion Baterie

~~CCS811~~

Oxygen

Kamera

~~As7265x~~

~~BHL1750~~

~~SD karta~~

~~LoRa~~

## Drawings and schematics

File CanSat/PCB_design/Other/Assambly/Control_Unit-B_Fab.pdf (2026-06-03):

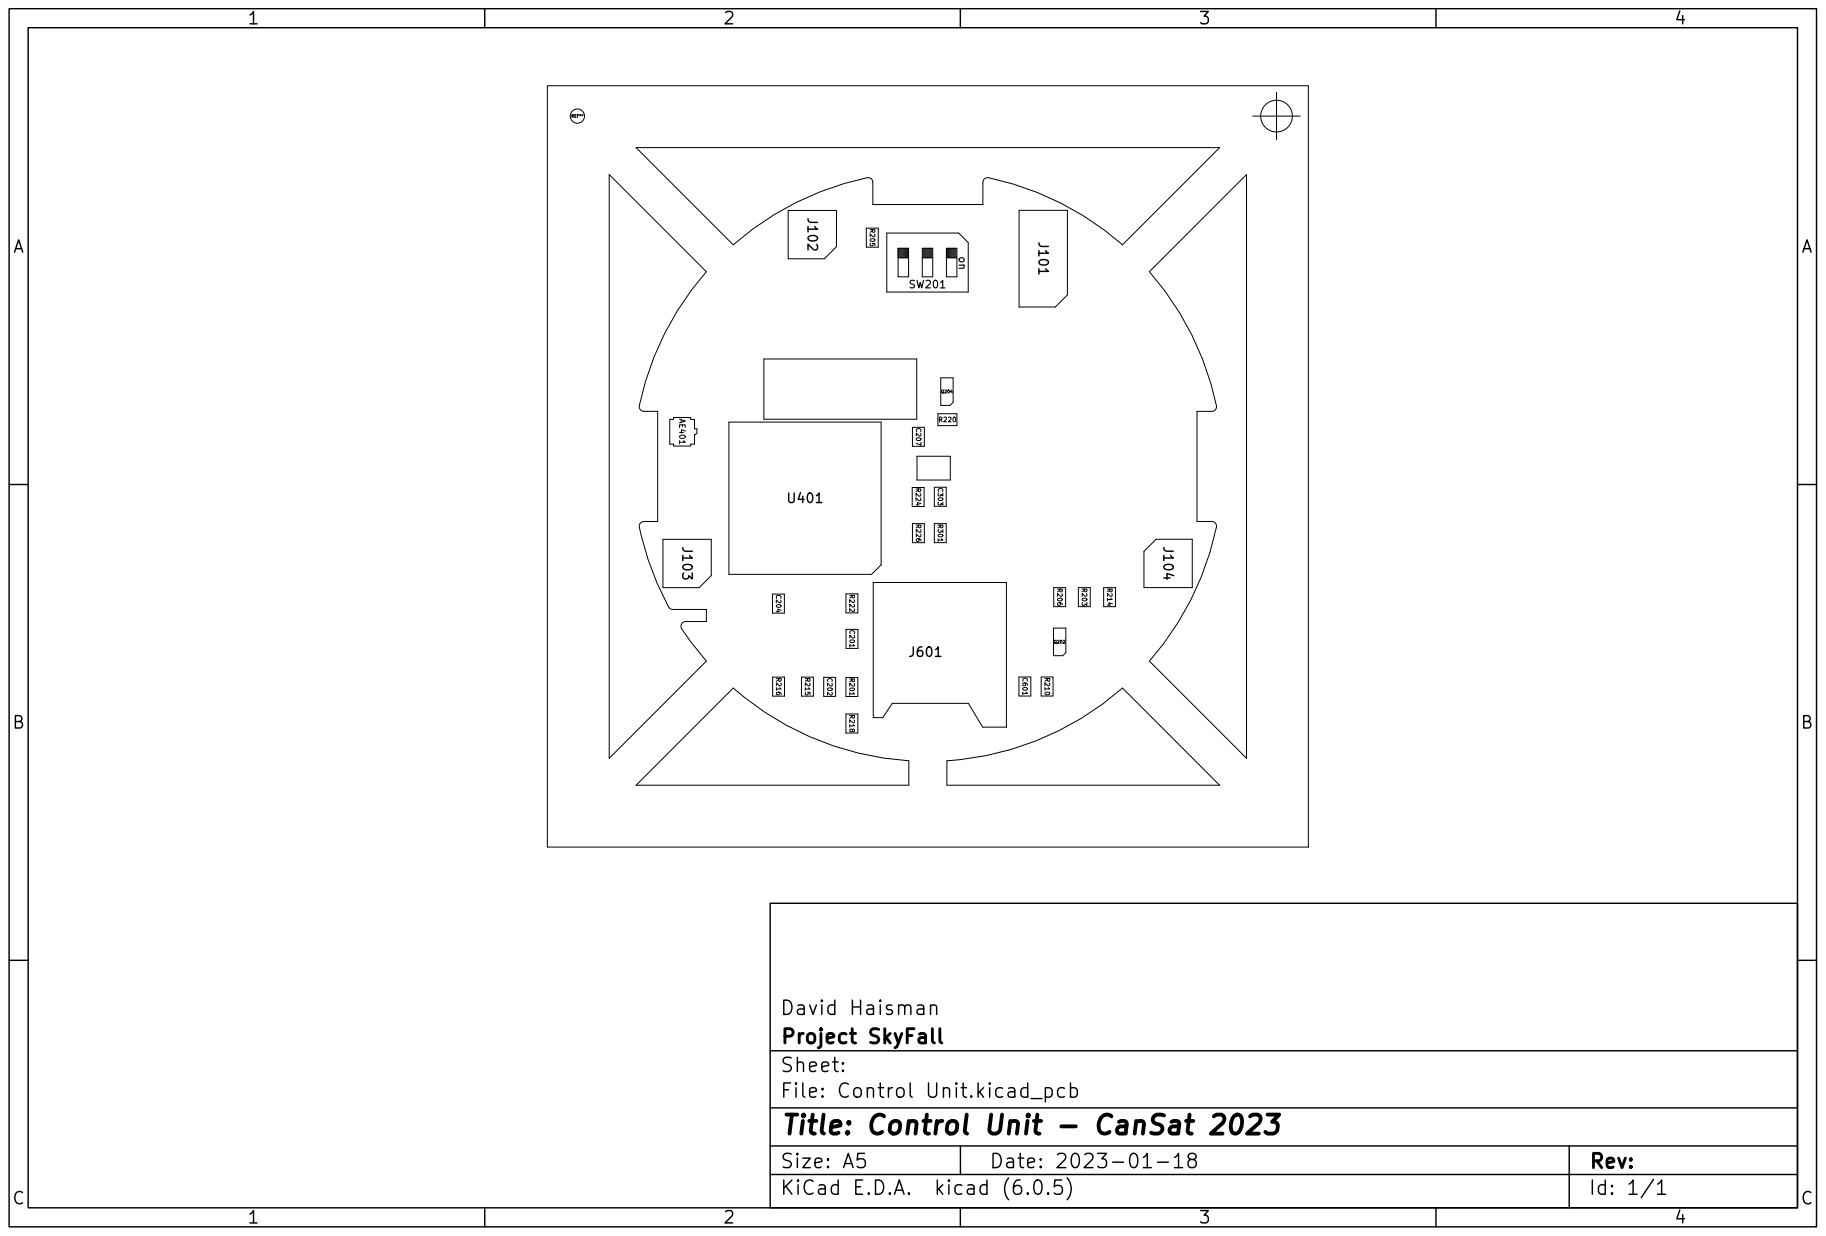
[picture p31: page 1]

File: Control Unit.kicad_pcb Sheet: Project SkyFall David Haisman

Id: 1/1 Title: Control Unit - CanSat 2023

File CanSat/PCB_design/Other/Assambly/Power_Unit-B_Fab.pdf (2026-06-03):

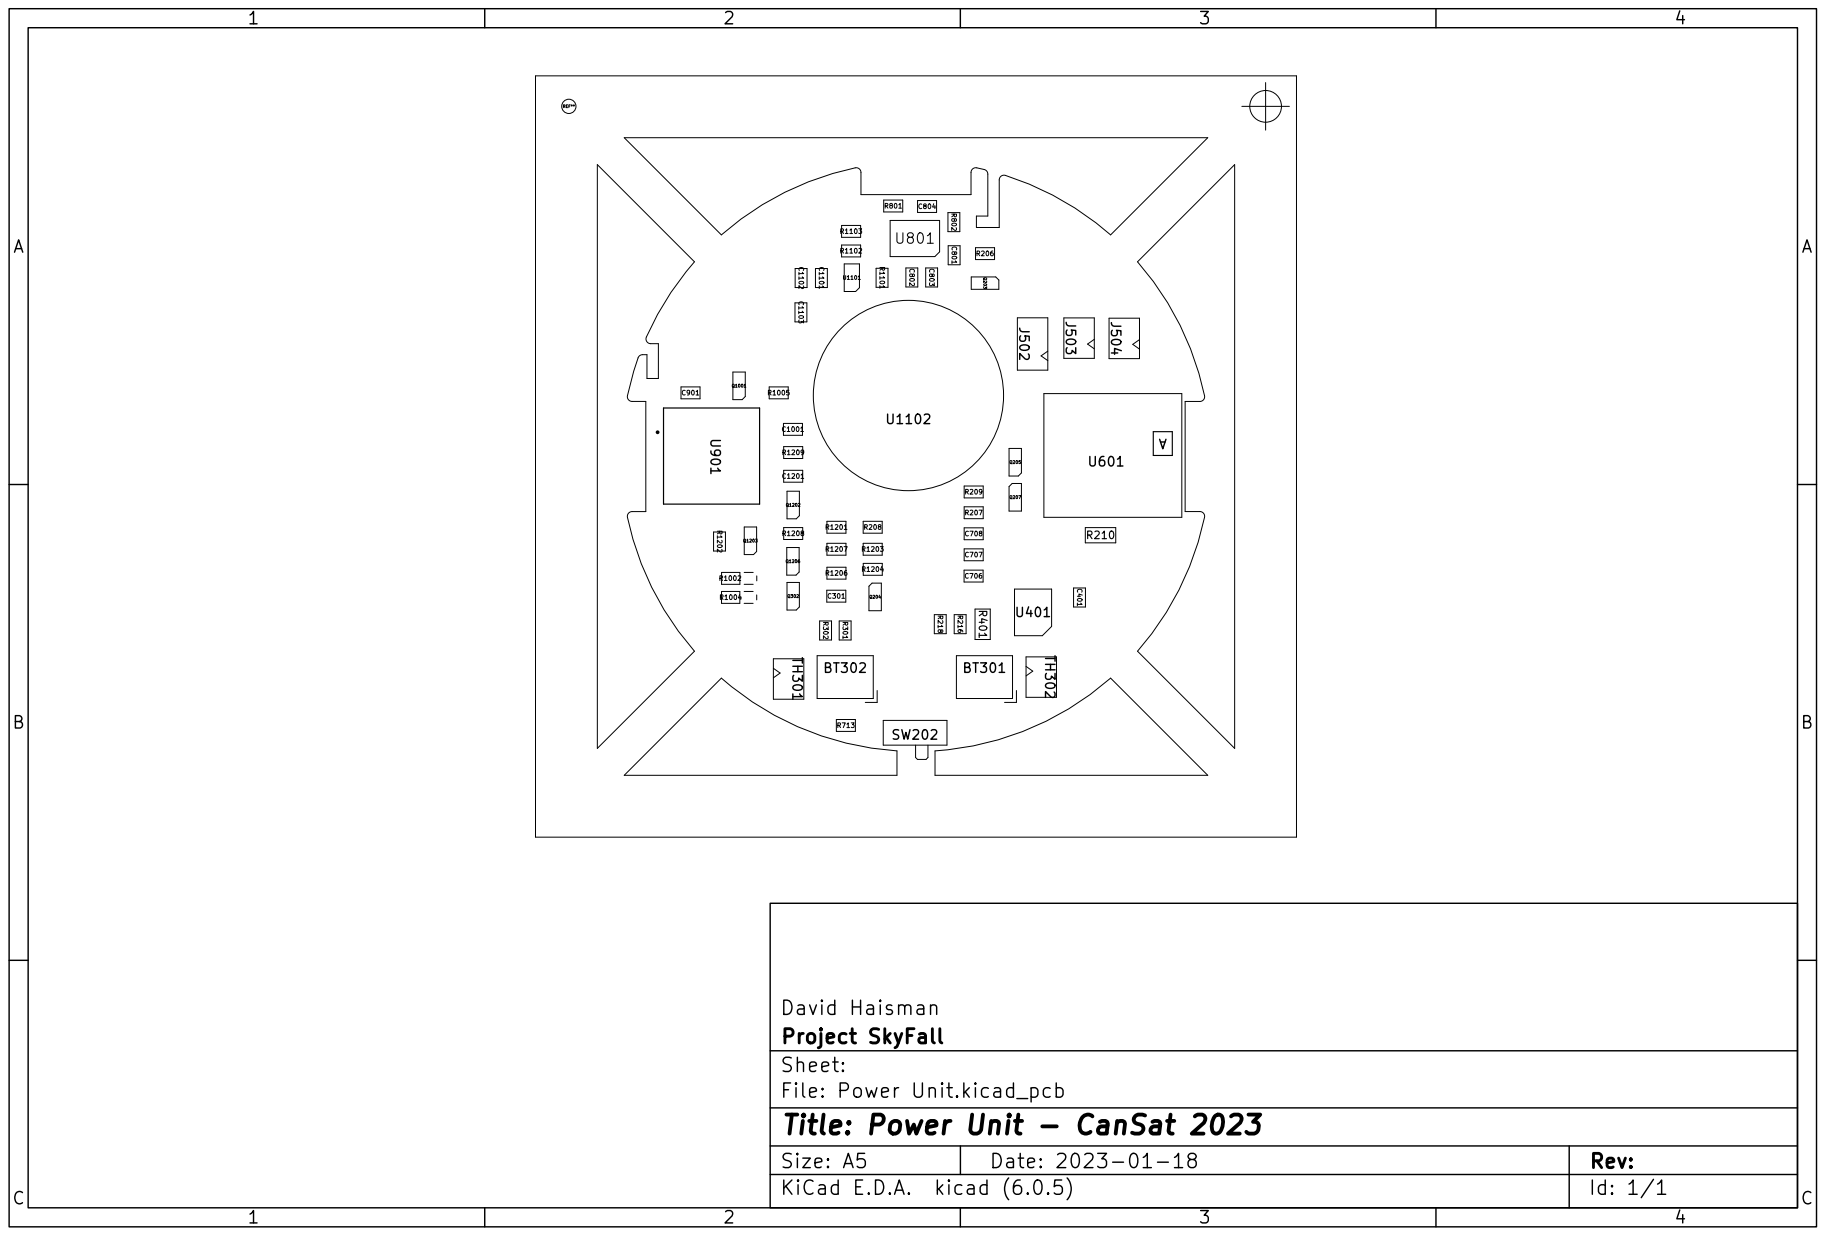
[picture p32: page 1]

Id: 1/1 Title: Power Unit - CanSat 2023

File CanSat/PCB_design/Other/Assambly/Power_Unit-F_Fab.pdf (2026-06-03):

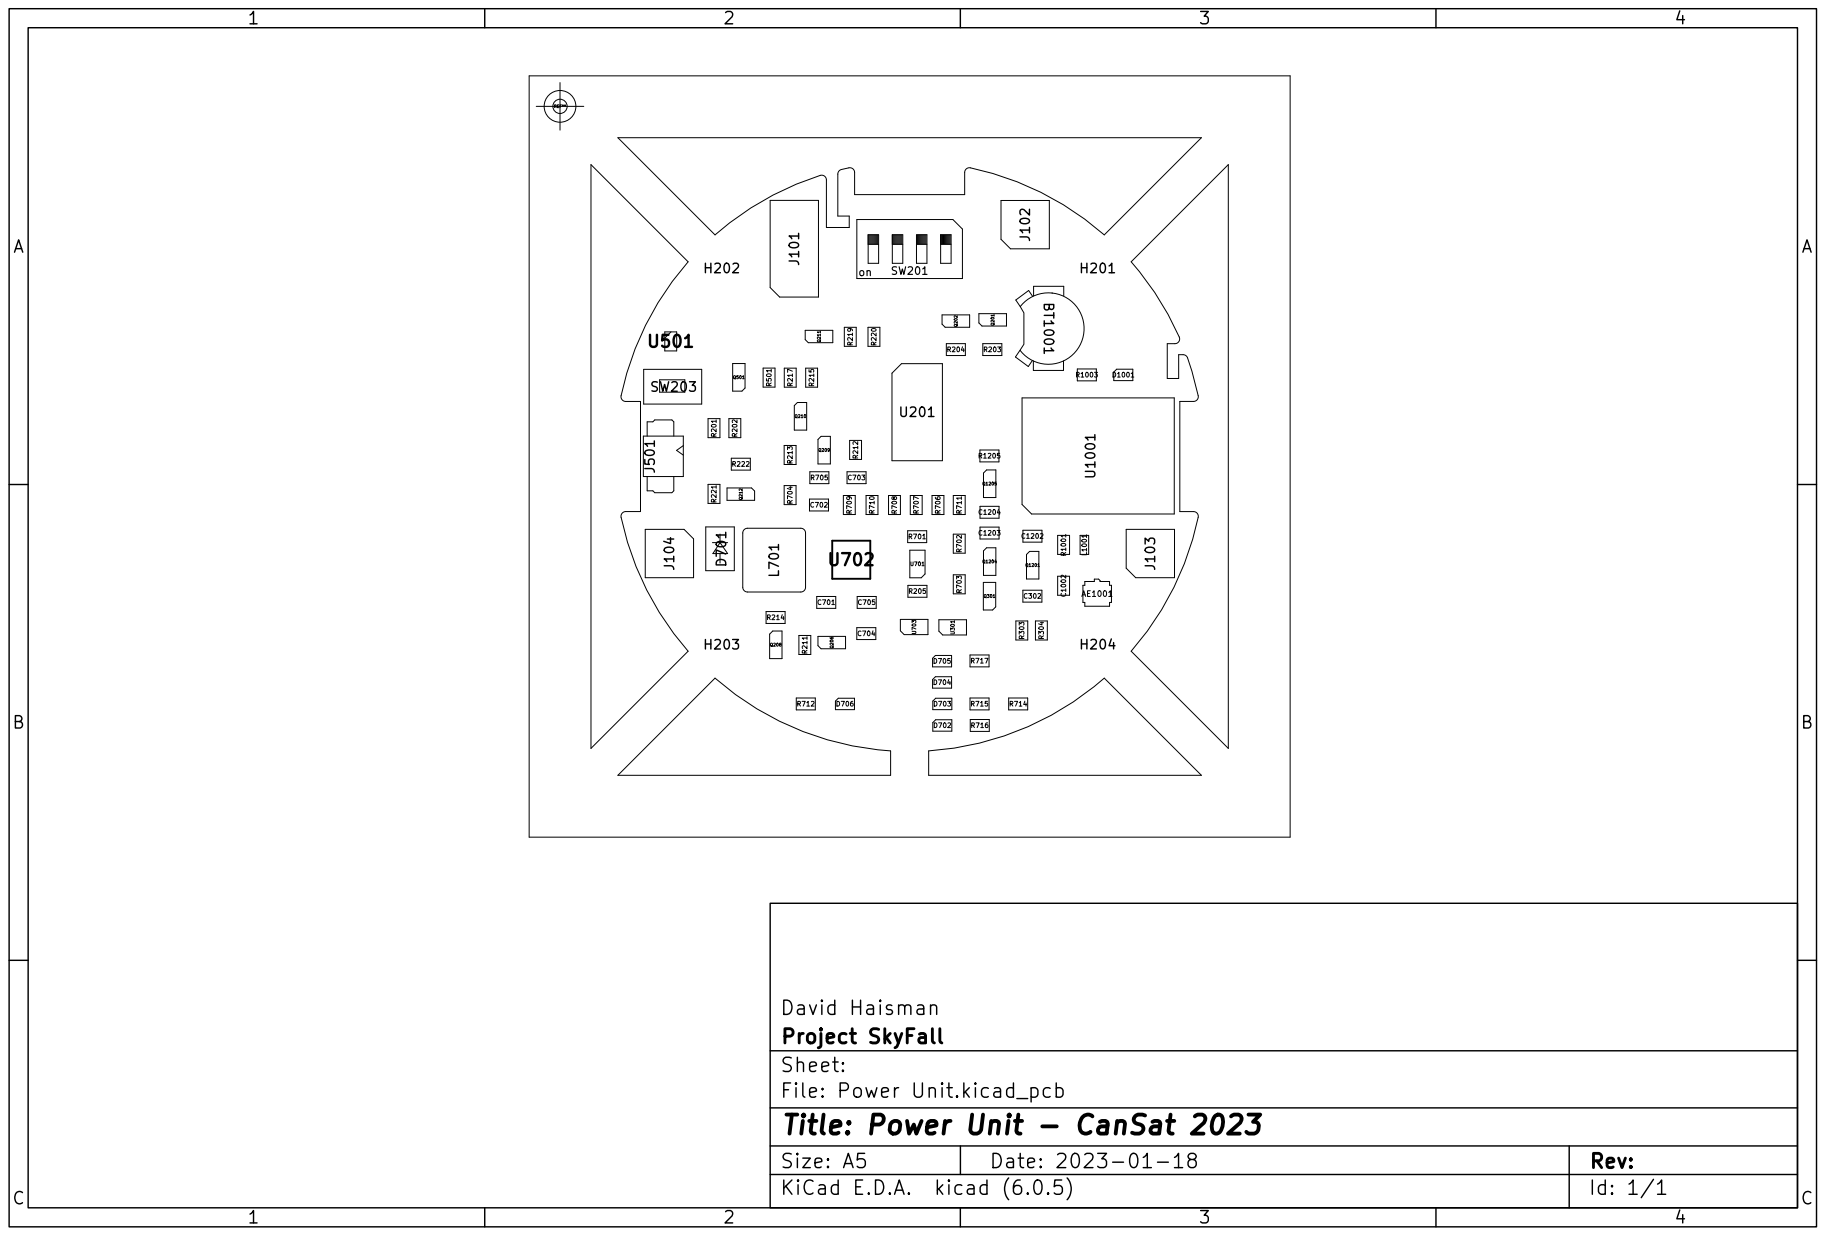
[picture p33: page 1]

File: Power Unit.kicad_pcb Sheet: Project SkyFall David Haisman

Id: 1/1 Title: Power Unit - CanSat 2023

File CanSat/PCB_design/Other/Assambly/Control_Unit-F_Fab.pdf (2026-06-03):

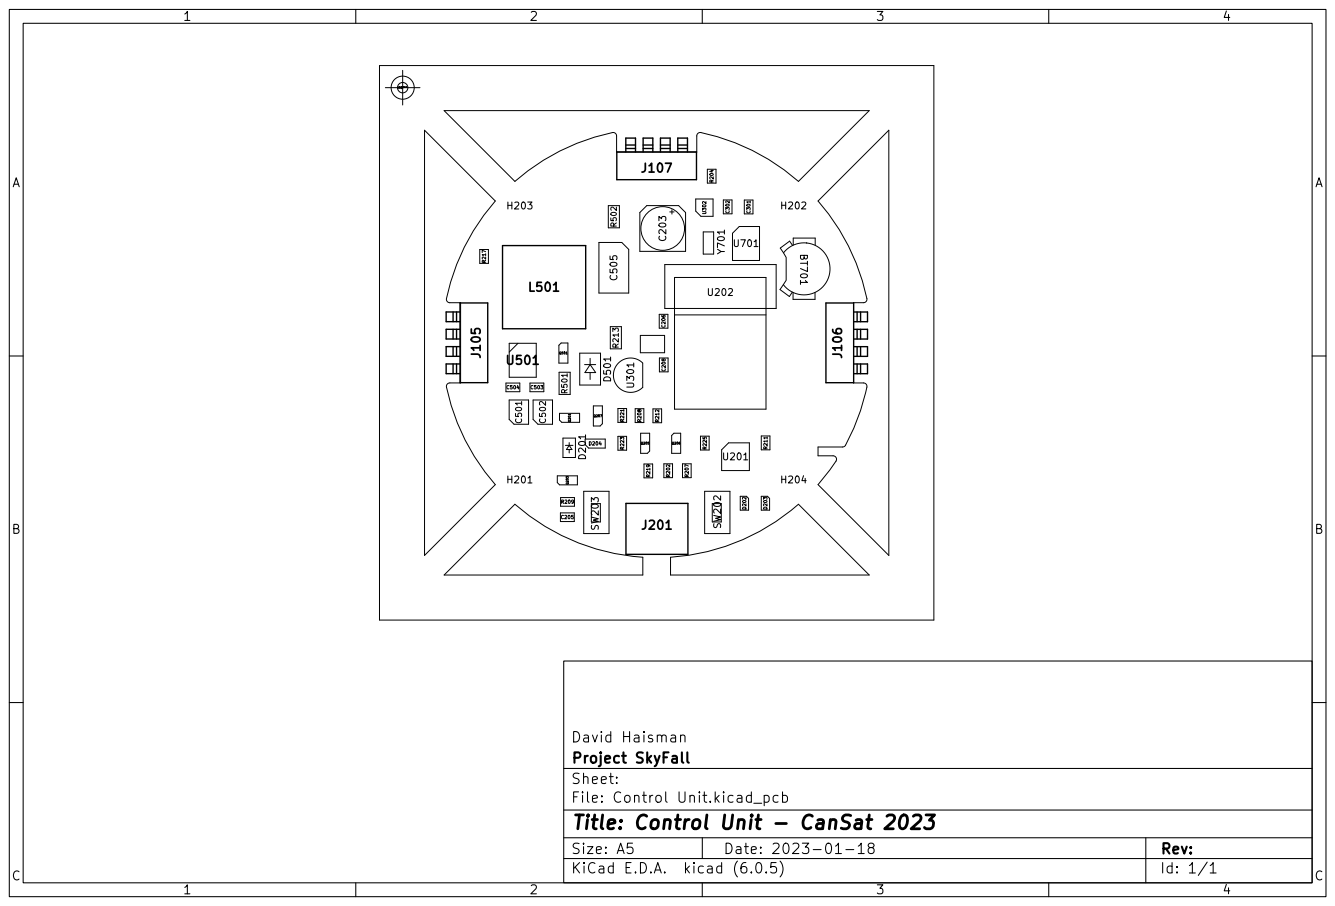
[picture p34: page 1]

Id: 1/1 Title: Control Unit - CanSat 2023

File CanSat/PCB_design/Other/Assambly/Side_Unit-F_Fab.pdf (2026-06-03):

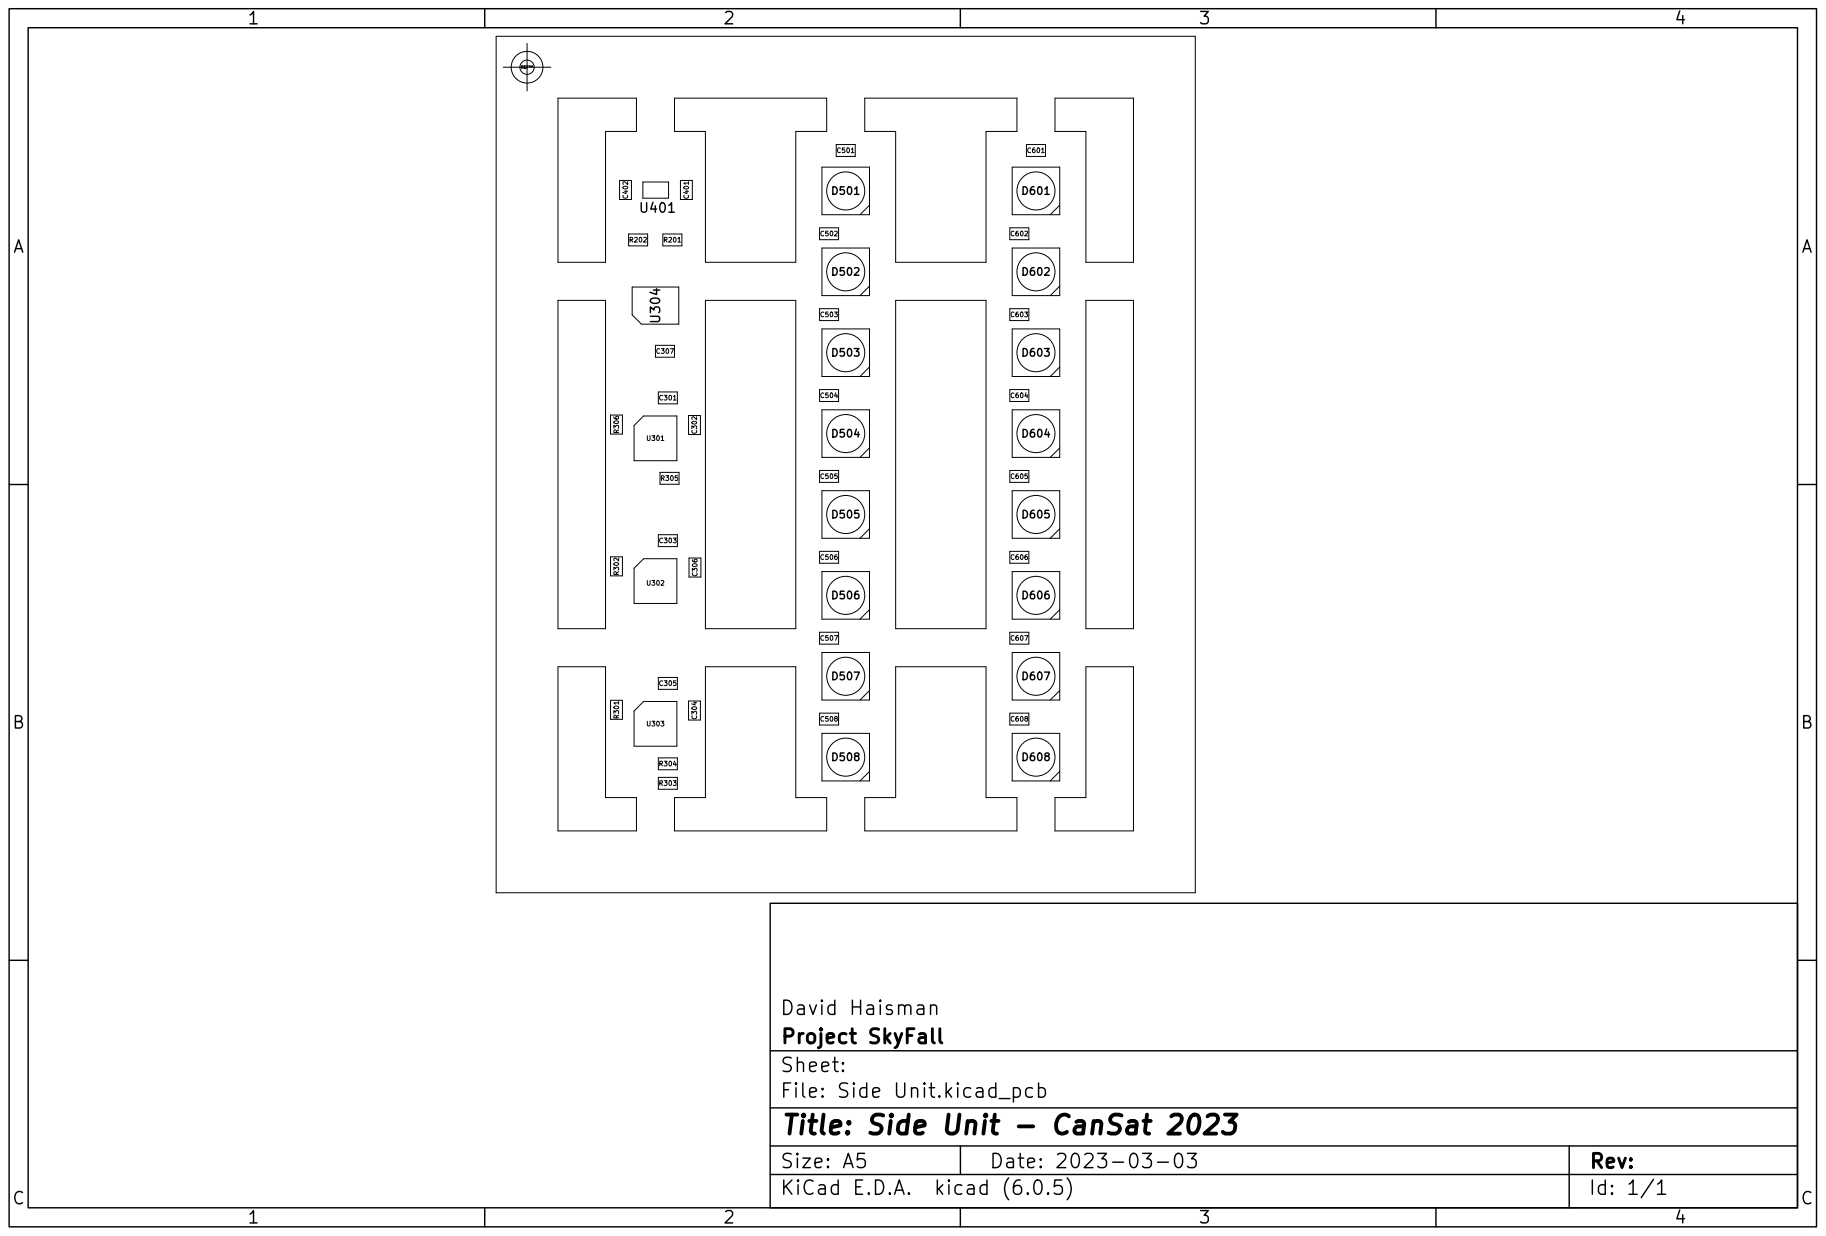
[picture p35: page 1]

Id: 1/1 Title: Side Unit - CanSat 2023

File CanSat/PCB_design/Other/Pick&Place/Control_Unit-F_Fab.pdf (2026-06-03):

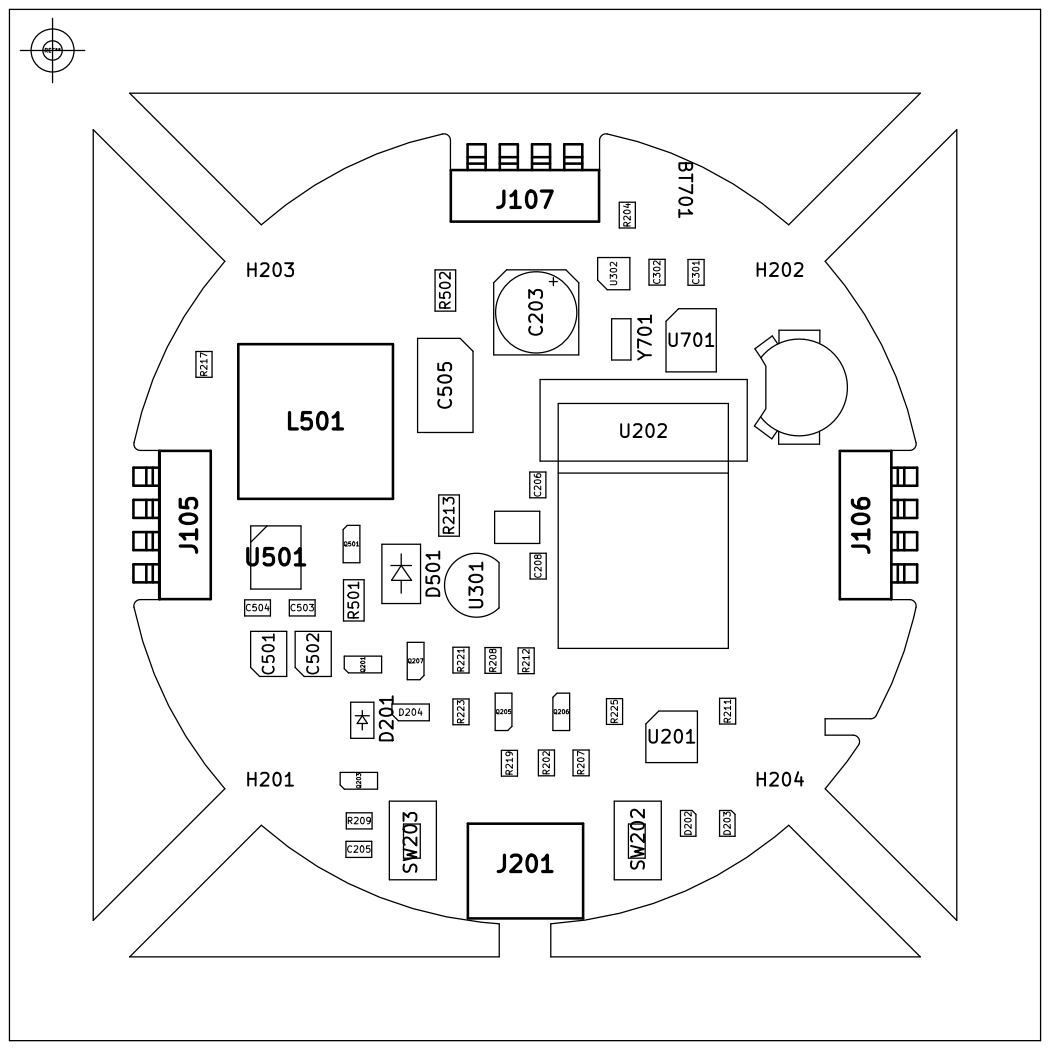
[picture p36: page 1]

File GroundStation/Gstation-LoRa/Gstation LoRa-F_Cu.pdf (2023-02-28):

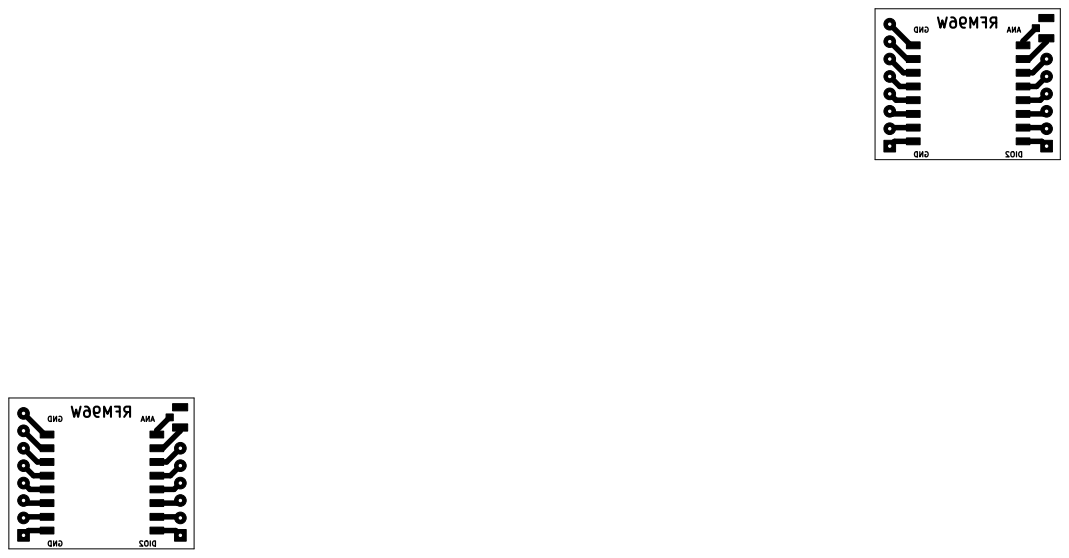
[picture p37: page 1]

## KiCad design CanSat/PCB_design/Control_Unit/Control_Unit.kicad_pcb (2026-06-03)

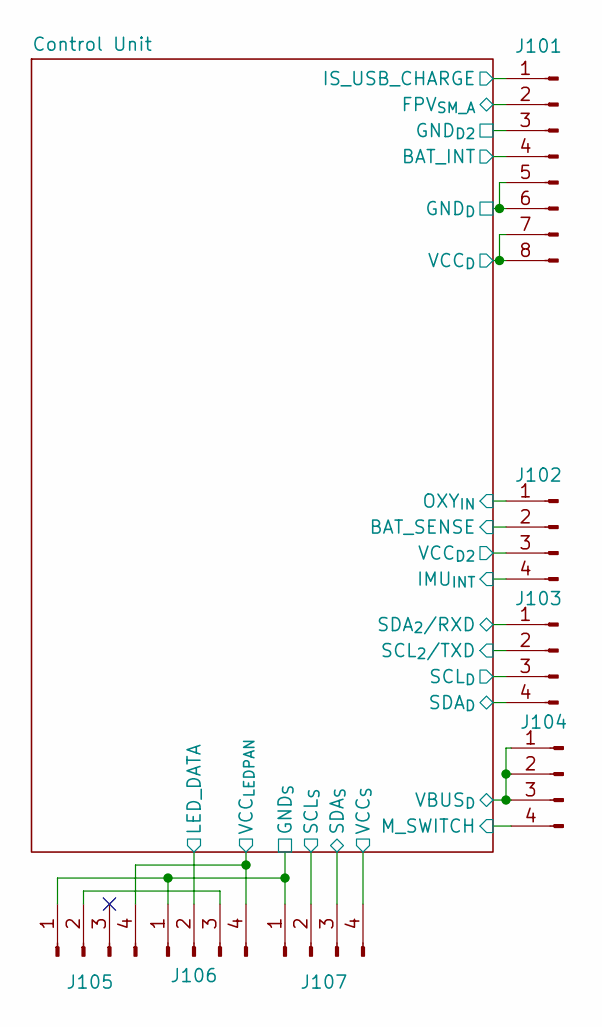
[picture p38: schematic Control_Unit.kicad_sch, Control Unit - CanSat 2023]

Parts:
J101: Conn_02x04_Male; PinHeader_2x04_P2.54mm_Vertical
J102, J103, J104: Conn_02x02_Male; PinHeader_2x02_P2.54mm_Vertical
J105, J106, J107: 009155004541006

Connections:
/Control Unit/BATT_INT: J101.4; also elsewhere on the board
/Control Unit/BAT_SENSE: J102.2; also elsewhere on the board
/Control Unit/FPV_{SM_A}: J101.2; also elsewhere on the board
/Control Unit/GND: J101.3, J101.5, J101.6, J105.1, J106.1, J107.1; also elsewhere on the board
/Control Unit/IMU_{INT}: J102.4; also elsewhere on the board
/Control Unit/IS_USB_CHARGE: J101.1; also elsewhere on the board
/Control Unit/LED_DATA: J106.2; also elsewhere on the board
/Control Unit/M_SWITCH: J104.4; also elsewhere on the board
/Control Unit/OXY_{IN}: J102.1; also elsewhere on the board
/Control Unit/SCL: J103.3, J107.2; also elsewhere on the board
/Control Unit/SCL_{2}/TXD: J103.2; also elsewhere on the board
/Control Unit/SDA: J103.4, J107.3; also elsewhere on the board
/Control Unit/SDA_{2}/RXD: J103.1; also elsewhere on the board
/Control Unit/VBUS: J104.1, J104.2, J104.3; also elsewhere on the board
/Control Unit/VCC: J101.7, J101.8, J102.3, J107.4; also elsewhere on the board
/Control Unit/VCC_{LEDPAN}: J105.4, J106.4; also elsewhere on the board
unnamed: J105.2, J106.3

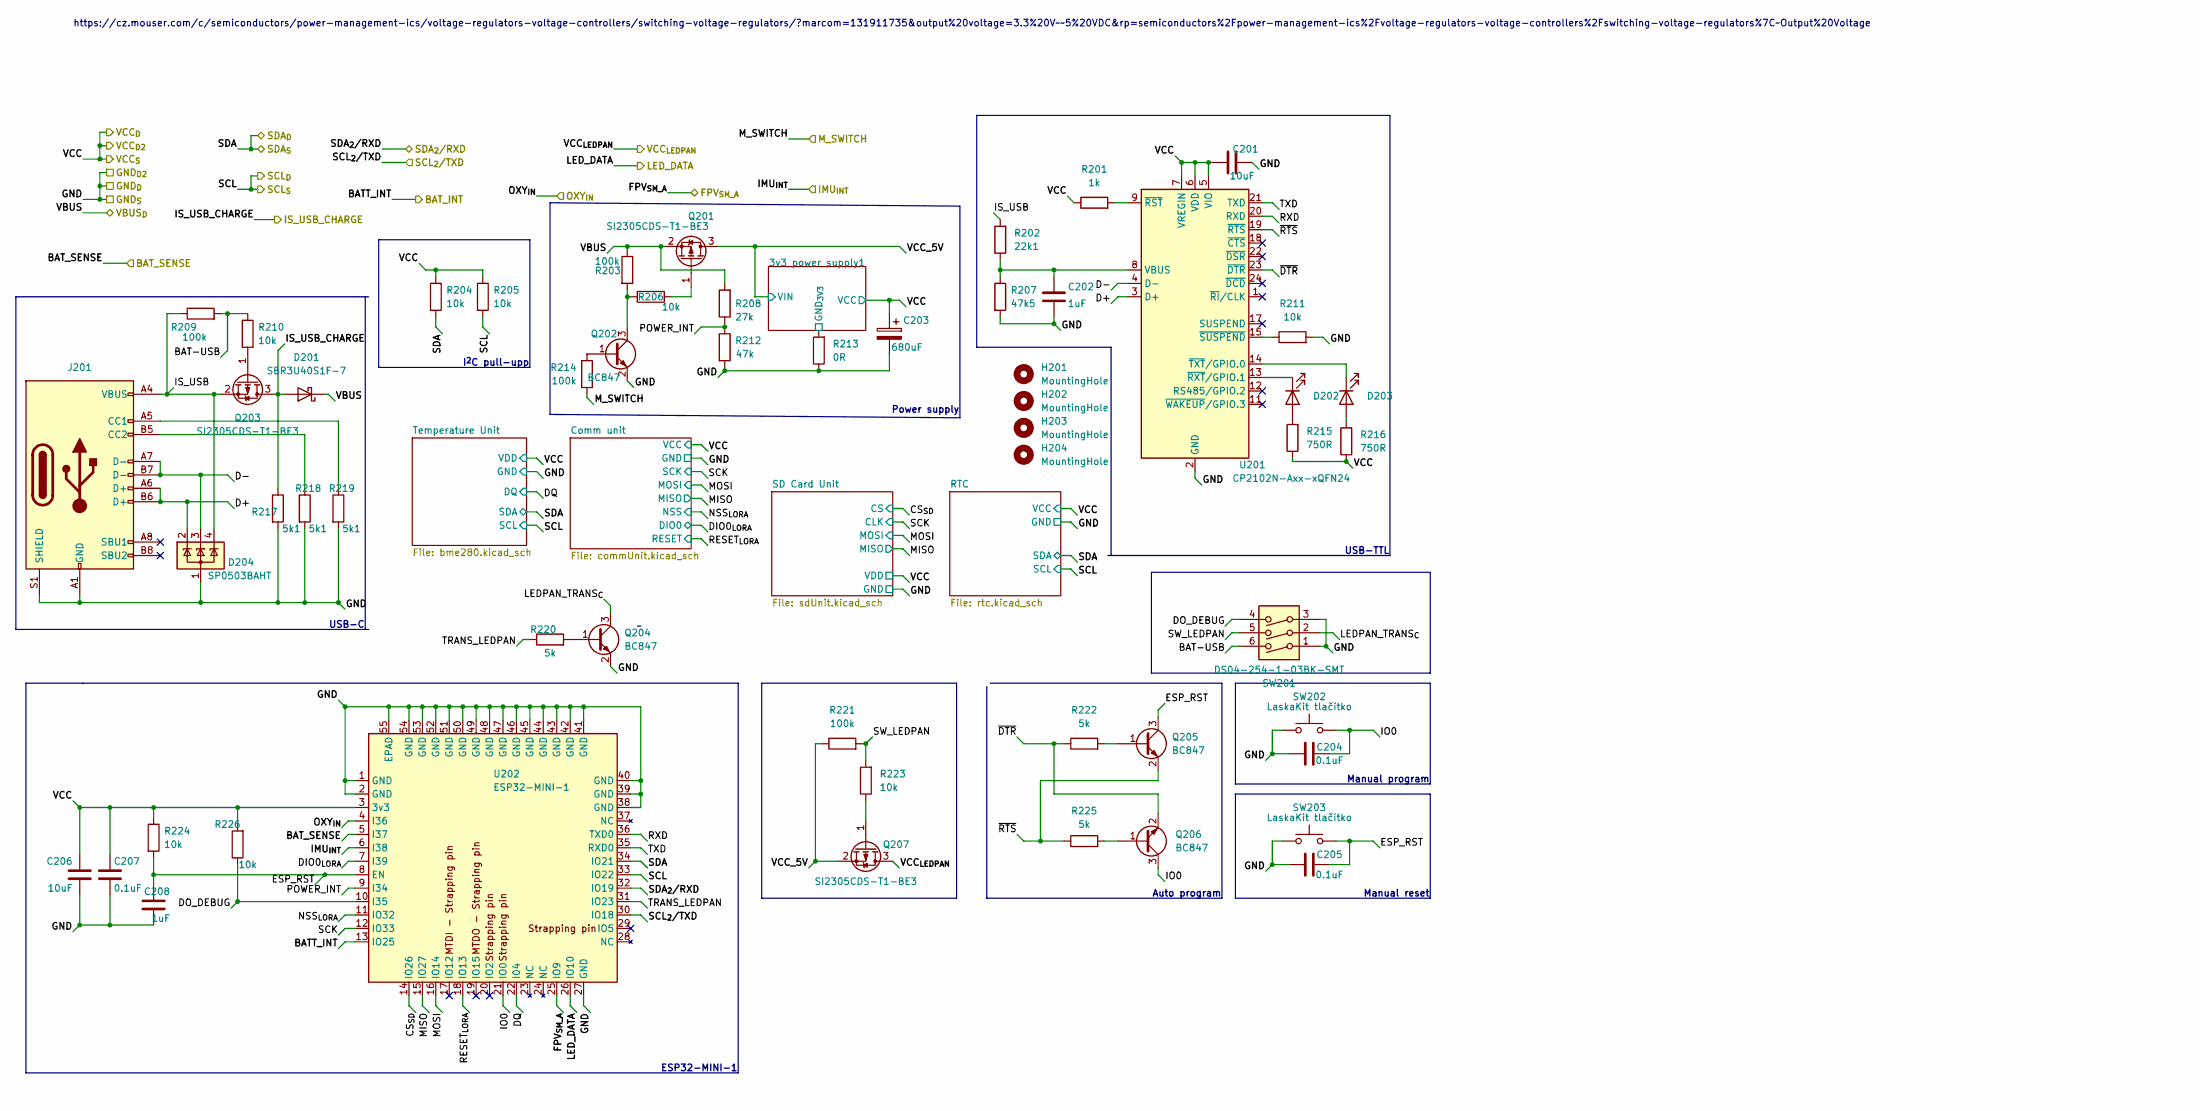
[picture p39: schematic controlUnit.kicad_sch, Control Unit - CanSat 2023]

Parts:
C201, C206: 10uF; C_0805_2012Metric
C202, C208: 1uF; C_0805_2012Metric
C203: 680uF; CP_Elec_6.3x7.7
C204, C205, C207: 0.1uF; C_0805_2012Metric
D201: SBR3U40S1F-7; D_SOD-123F
D202, D203: APT2012LSECK/J4-PRV; LED_0805_2012Metric
D204: SP0503BAHT; SOT-143
H201, H202, H203, H204: MountingHole; MountingHole_3.2mm_M3
J201: USB4110-GF-A; USB4110GFA
Q201, Q203, Q207: SI2305CDS-T1-BE3; SOT-23
Q202, Q204, Q205, Q206: BC847; SOT-23
R201: 1k; R_0805_2012Metric
R202: 22k1; R_0805_2012Metric
R203, R209, R214, R221: 100k; R_0805_2012Metric
R204, R205, R206, R210, R211, R223, R224, R226: 10k; R_0805_2012Metric
R207: 47k5; R_0805_2012Metric
R208: 27k; R_0805_2012Metric
R212: 47k; R_0805_2012Metric
R213: 0R; R_1206_3216Metric
R215, R216: 750R; R_0805_2012Metric
R217, R218, R219: 5k1; R_0805_2012Metric
R220, R222, R225: 5k; R_0805_2012Metric
SW201: DS04-254-1-03BK-SMT; SW_DIP_SPSTx03_Slide_Omron_A6S-310x_W8.9mm_P2.54mm
SW202, SW203: LaskaKit tlačítko; Tlačítko SMD LaskaKit
U201: CP2102N-Axx-xQFN24; QFN-24-1EP_4x4mm_P0.5mm_EP2.6x2.6mm
U202: ESP32-MINI-1

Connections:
/Control Unit/3v3 power supply1/GND_{3V3}: R213.2; also elsewhere on the board
/Control Unit/BAT-USB: R209.2, R210.1, SW201.6
/Control Unit/BATT_INT: U202.13 (IO25); also elsewhere on the board
/Control Unit/BAT_SENSE: U202.5 (I37); also elsewhere on the board
/Control Unit/CS_{SD}: U202.14 (IO26); also elsewhere on the board
/Control Unit/D+: D204.2 (K), J201.A6 (D+), J201.B6 (D+), U201.3 (D+)
/Control Unit/D-: D204.3 (K), J201.A7 (D-), J201.B7 (D-), U201.4 (D-)
/Control Unit/DIO0_{LORA}: U202.7 (I39); also elsewhere on the board
/Control Unit/DO_DEBUG: R226.1, SW201.4, U202.10 (I35)
/Control Unit/DQ: U202.22 (I04); also elsewhere on the board
/Control Unit/ESP_RST: C205.2, C208.1, Q205.3 (C), R224.2, SW203.2, U202.8 (EN)
/Control Unit/FPV_{SM_A}: U202.25 (IO9); also elsewhere on the board
/Control Unit/GND: C201.2, C202.2, C203.2, C204.1, C205.1, C206.2, C207.2, C208.2, D204.1 (A), J201.A1 (GND), J201.A12 (GND), J201.B1 (GND), J201.B12 (GND), J201.S1 (SHIELD), Q202.2 (E), Q204.2 (E), R207.2, R211.2, R212.2, R213.1, R217.2, R218.2, R219.2, SW201.1, SW201.3, SW202.1, SW203.1, U201.2 (GND), U201.25 (GND), U202.1 (GND), U202.2 (GND), U202.27 (GND), U202.38 (GND), U202.39 (GND), U202.40 (GND), U202.41 (GND), U202.42 (GND), U202.43 (GND), U202.44 (GND), U202.45 (GND), U202.46 (GND), U202.47 (GND), U202.48 (GND), U202.49 (GND), U202.50 (GND), U202.51 (GND), U202.52 (GND), U202.53 (GND), U202.54 (GND), U202.55 (EPAD); also elsewhere on the board
/Control Unit/IMU_{INT}: U202.6 (I38); also elsewhere on the board
/Control Unit/IO0: C204.2, Q206.3 (C), SW202.2, U202.21 (IO0)
/Control Unit/IS_USB: D204.4 (K), J201.A4 (VBUS), J201.A9 (VBUS), J201.B4 (VBUS), J201.B9 (VBUS), Q203.2 (S), R202.2, R209.1
/Control Unit/IS_USB_CHARGE: D201.2 (A), Q203.3 (D), R217.1; also elsewhere on the board
/Control Unit/LEDPAN_TRANS_{C}: Q204.3 (C), SW201.2
/Control Unit/LED_DATA: U202.26 (IO10); also elsewhere on the board
/Control Unit/MISO: U202.15 (IO27); also elsewhere on the board
/Control Unit/MOSI: U202.16 (IO14); also elsewhere on the board
/Control Unit/M_SWITCH: R214.1; also elsewhere on the board
/Control Unit/NSS_{LORA}: U202.11 (IO32); also elsewhere on the board
/Control Unit/OXY_{IN}: U202.4 (I36); also elsewhere on the board
/Control Unit/POWER_INT: R208.1, R212.1, U202.9 (I34)
/Control Unit/RESET_{LORA}: U202.18 (IO13); also elsewhere on the board
/Control Unit/RXD: U201.20 (RXD), U202.36 (TXD0)
/Control Unit/SCK: U202.12 (IO33); also elsewhere on the board
/Control Unit/SCL: R205.2, U202.33 (IO22); also elsewhere on the board
/Control Unit/SCL_{2}/TXD: U202.30 (IO18); also elsewhere on the board
/Control Unit/SDA: R204.2, U202.34 (IO21); also elsewhere on the board
/Control Unit/SDA_{2}/RXD: U202.32 (IO19); also elsewhere on the board
/Control Unit/SW_LEDPAN: R221.2, R223.2, SW201.5
/Control Unit/TRANS_LEDPAN: R220.1, U202.31 (IO23)
/Control Unit/TXD: U201.21 (TXD), U202.35 (RXD0)
/Control Unit/VBUS: D201.1 (K), Q201.2 (S), R203.1, R208.2; also elsewhere on the board
/Control Unit/VCC: C201.1, C203.1, C206.1, C207.1, R201.1, R204.1, R205.1, R215.1, R216.1, R224.1, R226.2, U201.5 (VIO), U201.6 (VDD), U201.7 (VREGIN), U202.3 (3v3); also elsewhere on the board
/Control Unit/VCC_5V: Q201.3 (D), Q207.2 (S), R221.1; also elsewhere on the board
/Control Unit/VCC_{LEDPAN}: Q207.3 (D); also elsewhere on the board
/Control Unit/~DTR: Q206.2 (E), R222.1, U201.23 (~DTR)
/Control Unit/~RTS: Q205.2 (E), R225.1, U201.19 (~RTS)
unnamed: C202.1, R202.1, R207.1, U201.8 (VBUS)
unnamed: D202.1 (K), U201.13 (~RXT/GPIO.1)
unnamed: D202.2 (A), R215.2
unnamed: D203.1 (K), U201.14 (~TXT/GPIO.0)
unnamed: D203.2 (A), R216.2
unnamed: J201.A5 (CC1), R219.1
unnamed: J201.B5 (CC2), R218.1
unnamed: Q201.1 (G), R206.1
unnamed: Q202.1 (B), R214.2
unnamed: Q202.3 (C), R203.2, R206.2
unnamed: Q203.1 (G), R210.2
unnamed: Q204.1 (B), R220.2
unnamed: Q205.1 (B), R222.2
unnamed: Q206.1 (B), R225.2
unnamed: Q207.1 (G), R223.1
unnamed: R201.2, U201.9 (~RST)
unnamed: R211.1, U201.15 (~SUSPEND)

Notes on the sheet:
USB-TTL
I^{2}C pull-upp
Auto program
ESP32-MINI-1
USB-C
Power supply
Manual reset
https://cz.mouser.com/c/semiconductors/power-management-ics/voltage-regulators-voltage-controllers/switching-voltage-regulators/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…
Manual program

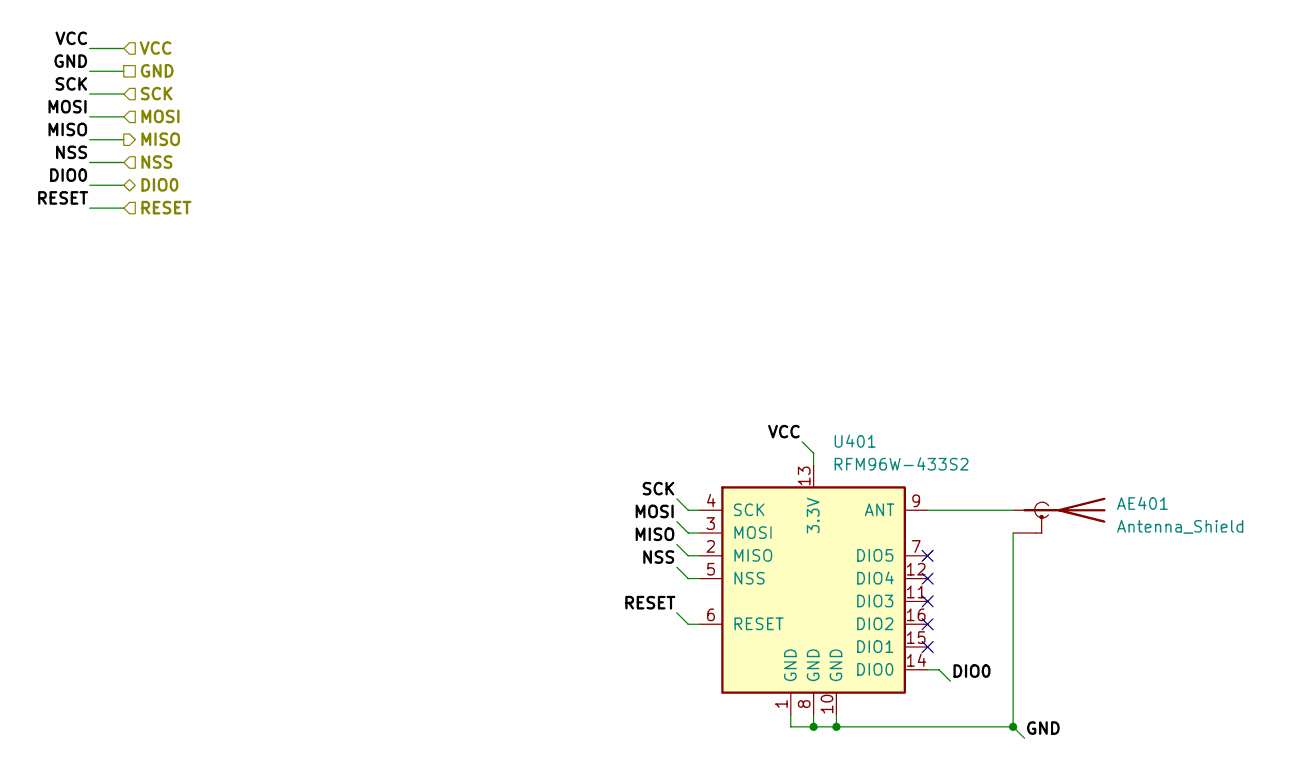
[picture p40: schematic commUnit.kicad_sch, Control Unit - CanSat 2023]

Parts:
AE401: Antenna_Shield; U.FL_Hirose_U.FL-R-SMT-1_Vertical
U401: RFM96W-433S2; HOPERF_RFM9XW_SMD

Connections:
/Control Unit/DIO0_{LORA}: U401.14 (DIO0); also elsewhere on the board
/Control Unit/GND: AE401.2 (Shield), U401.1 (GND), U401.8 (GND), U401.10 (GND); also elsewhere on the board
/Control Unit/MISO: U401.2 (MISO); also elsewhere on the board
/Control Unit/MOSI: U401.3 (MOSI); also elsewhere on the board
/Control Unit/NSS_{LORA}: U401.5 (NSS); also elsewhere on the board
/Control Unit/RESET_{LORA}: U401.6 (RESET); also elsewhere on the board
/Control Unit/SCK: U401.4 (SCK); also elsewhere on the board
/Control Unit/VCC: U401.13 (3.3V); also elsewhere on the board
unnamed: AE401.1 (A), U401.9 (ANT)

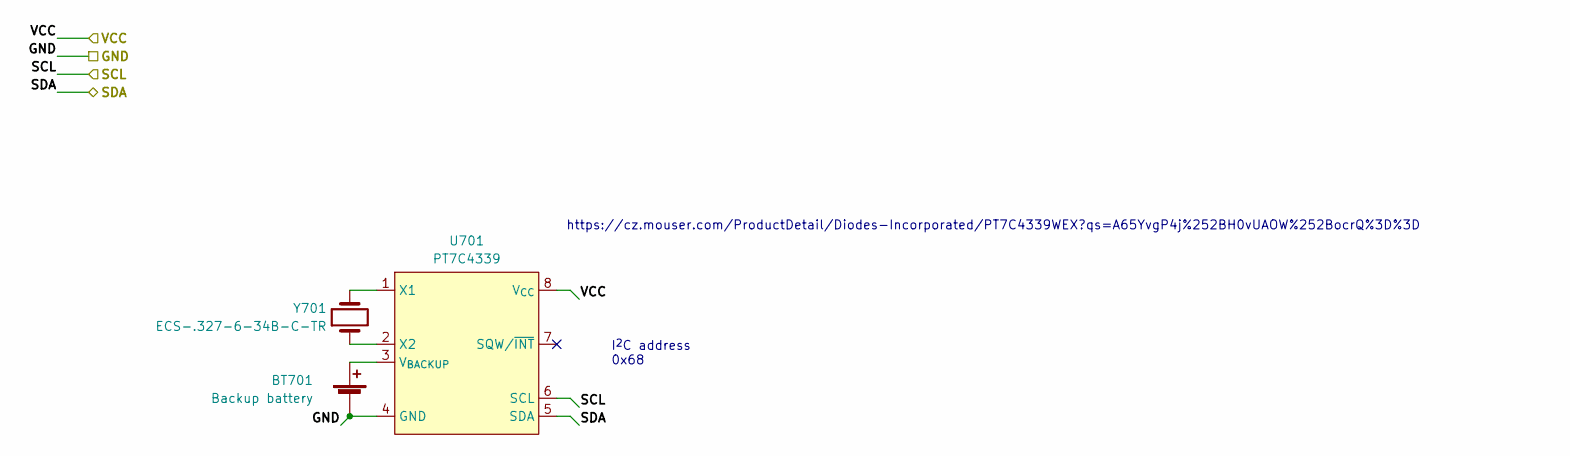
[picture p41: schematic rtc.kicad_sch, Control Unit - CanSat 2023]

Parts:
BT701: Backup battery; 2989
U701: PT7C4339; SOIC-8-1EP_3.9x4.9mm_P1.27mm_EP2.29x3mm
Y701: ECS-.327-6-34B-C-TR; ECX-31B

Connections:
/Control Unit/GND: BT701.2 (-), U701.4 (GND); also elsewhere on the board
/Control Unit/SCL: U701.6 (SCL); also elsewhere on the board
/Control Unit/SDA: U701.5 (SDA); also elsewhere on the board
/Control Unit/VCC: U701.8 (V_{CC}); also elsewhere on the board
unnamed: BT701.1 (+), U701.3 (V_{BACKUP})
unnamed: U701.1 (X1), Y701.2
unnamed: U701.2 (X2), Y701.1

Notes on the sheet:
https://cz.mouser.com/ProductDetail/Diodes-Incorporated/PT7C4339WEX?qs=A65YvgP4j%252BH0vUAOW%252BocrQ%3D%3D
I^{2}C address 0x68

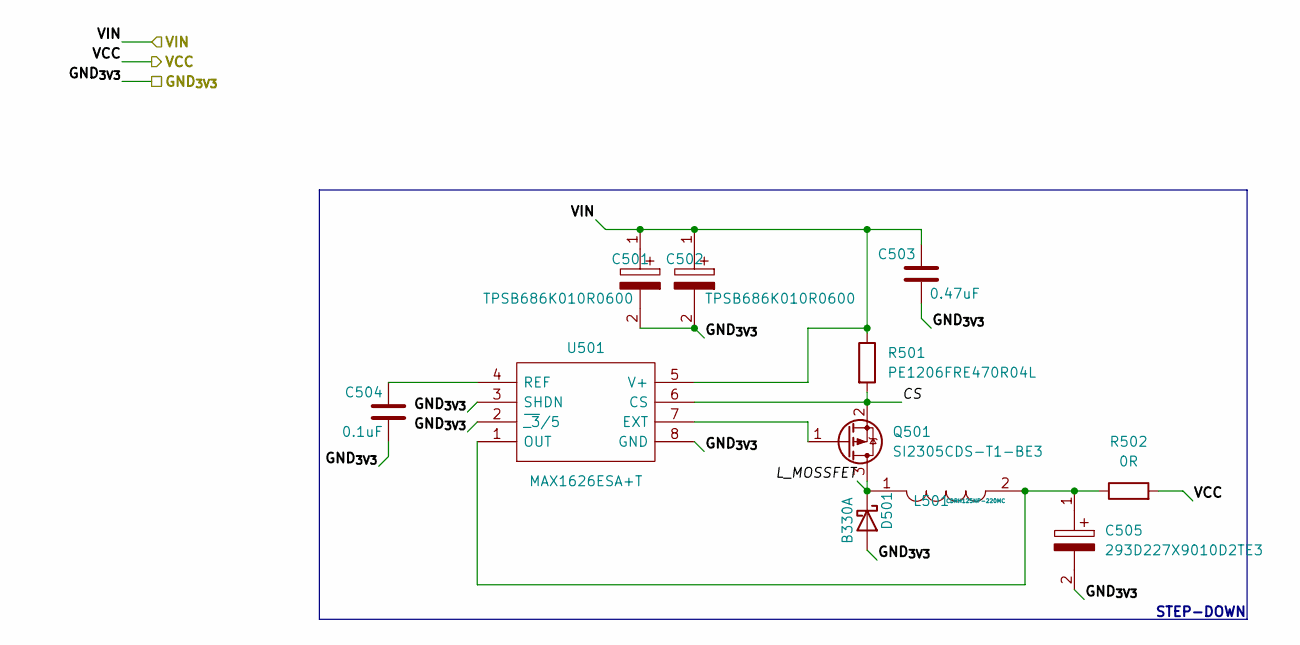
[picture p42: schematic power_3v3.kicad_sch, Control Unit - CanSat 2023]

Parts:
C501, C502: TPSB686K010R0600; CP_EIA-3528-21_Kemet-B; Mouser Part Number 581-TPSB686K010R0600
C503: 0.47uF; C_0805_2012Metric
C504: 0.1uF; C_0805_2012Metric
C505: 293D227X9010D2TE3; CP_EIA-7343-31_Kemet-D; Mouser Part Number 74-293D227X9010D2TE3
D501: B330A; D_SMA
L501: CDRH125NP-220MC; CDRH125101MC; Mouser Part Number 851-CDRH125NP-220MC
Q501: SI2305CDS-T1-BE3; SOT-23
R501: PE1206FRE470R04L; R_1206_Current
R502: 0R; R_1206_3216Metric
U501: MAX1626ESA+T; SOIC127P600X175-8N; Mouser Part Number 700-MAX1626ESAT

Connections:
/Control Unit/3v3 power supply1/CS: Q501.2 (S), R501.2, U501.6 (CS)
/Control Unit/3v3 power supply1/GND_{3V3}: C501.2, C502.2, C503.2, C504.2, C505.2, D501.2 (A), U501.2 (~_3/5), U501.3 (SHDN), U501.8 (GND); also elsewhere on the board
/Control Unit/3v3 power supply1/L_MOSSFET: D501.1 (K), L501.1, Q501.3 (D)
/Control Unit/VCC: R502.2; also elsewhere on the board
/Control Unit/VCC_5V: C501.1, C502.1, C503.1, R501.1, U501.5 (V+); also elsewhere on the board
unnamed: C504.1, U501.4 (REF)
unnamed: C505.1, L501.2, R502.1, U501.1 (OUT)
unnamed: Q501.1 (G), U501.7 (EXT)

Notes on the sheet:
STEP-DOWN

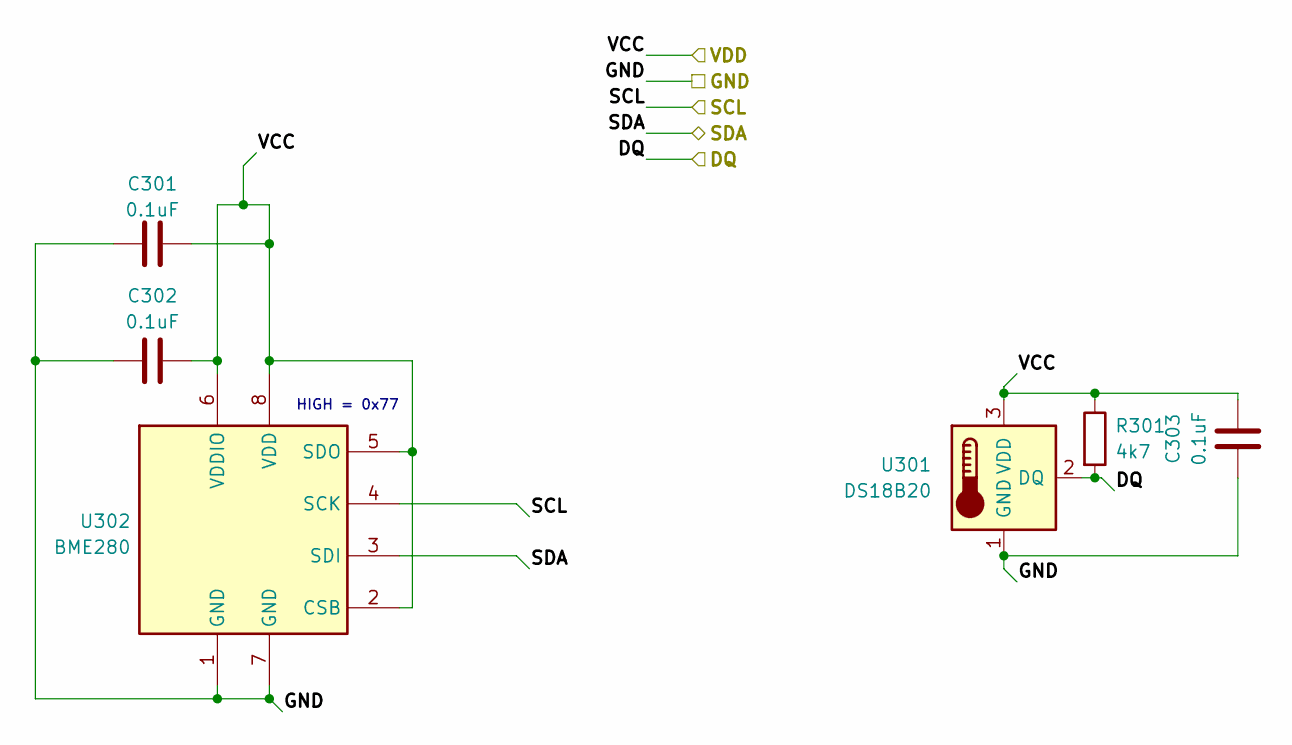
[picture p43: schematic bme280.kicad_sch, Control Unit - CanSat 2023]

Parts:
C301, C302, C303: 0.1uF; C_0805_2012Metric
R301: 4k7; R_0805_2012Metric
U301: DS18B20; TO-92_Inline
U302: BME280; Bosch_LGA-8_2.5x2.5mm_P0.65mm_ClockwisePinNumbering

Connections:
/Control Unit/DQ: R301.2, U301.2 (DQ); also elsewhere on the board
/Control Unit/GND: C301.2, C302.2, C303.2, U301.1 (GND), U302.1 (GND), U302.7 (GND); also elsewhere on the board
/Control Unit/SCL: U302.4 (SCK); also elsewhere on the board
/Control Unit/SDA: U302.3 (SDI); also elsewhere on the board
/Control Unit/VCC: C301.1, C302.1, C303.1, R301.1, U301.3 (VDD), U302.2 (CSB), U302.5 (SDO), U302.6 (VDDIO), U302.8 (VDD); also elsewhere on the board

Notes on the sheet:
HIGH = 0x77

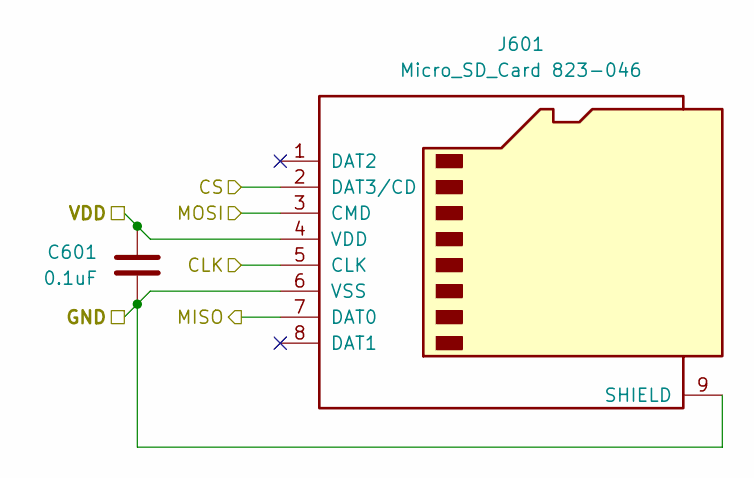
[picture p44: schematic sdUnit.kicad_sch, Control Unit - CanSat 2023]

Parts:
C601: 0.1uF; C_0805_2012Metric
J601: Micro_SD_Card 823-046; DS1139-05

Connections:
/Control Unit/CS_{SD}: J601.2 (DAT3/CD); also elsewhere on the board
/Control Unit/GND: C601.1, J601.6 (VSS), J601.9 (SHIELD); also elsewhere on the board
/Control Unit/MISO: J601.7 (DAT0); also elsewhere on the board
/Control Unit/MOSI: J601.3 (CMD); also elsewhere on the board
/Control Unit/SCK: J601.5 (CLK); also elsewhere on the board
/Control Unit/VCC: C601.2, J601.4 (VDD); also elsewhere on the board

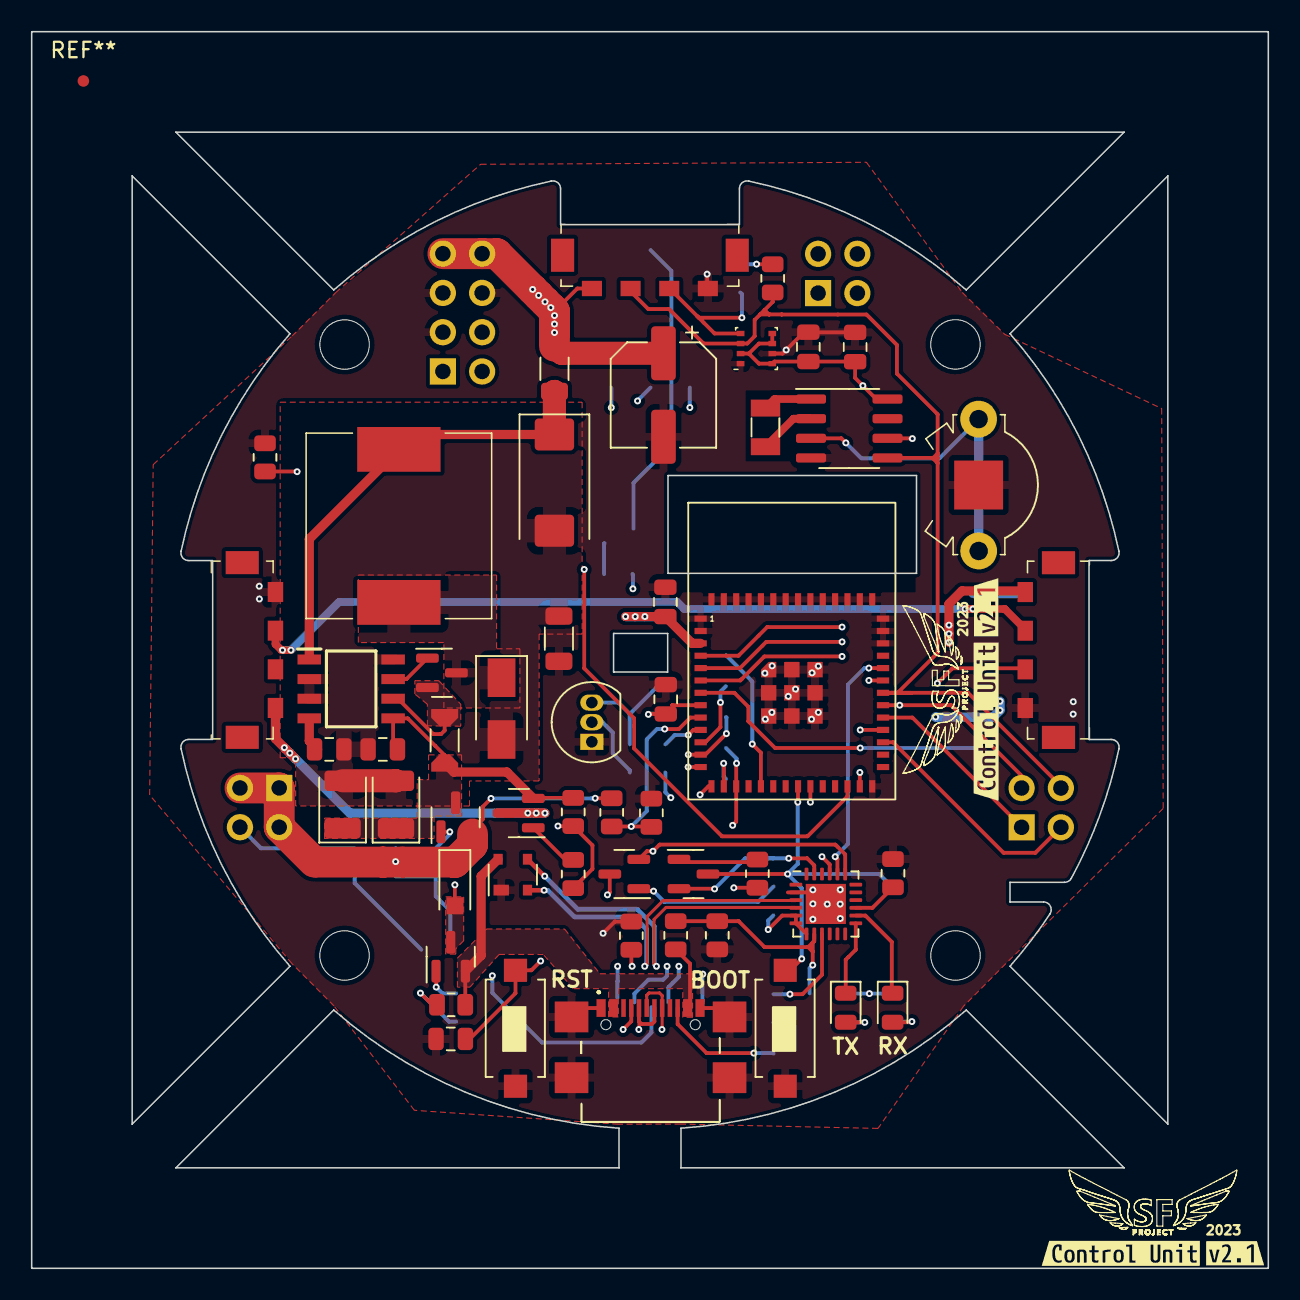
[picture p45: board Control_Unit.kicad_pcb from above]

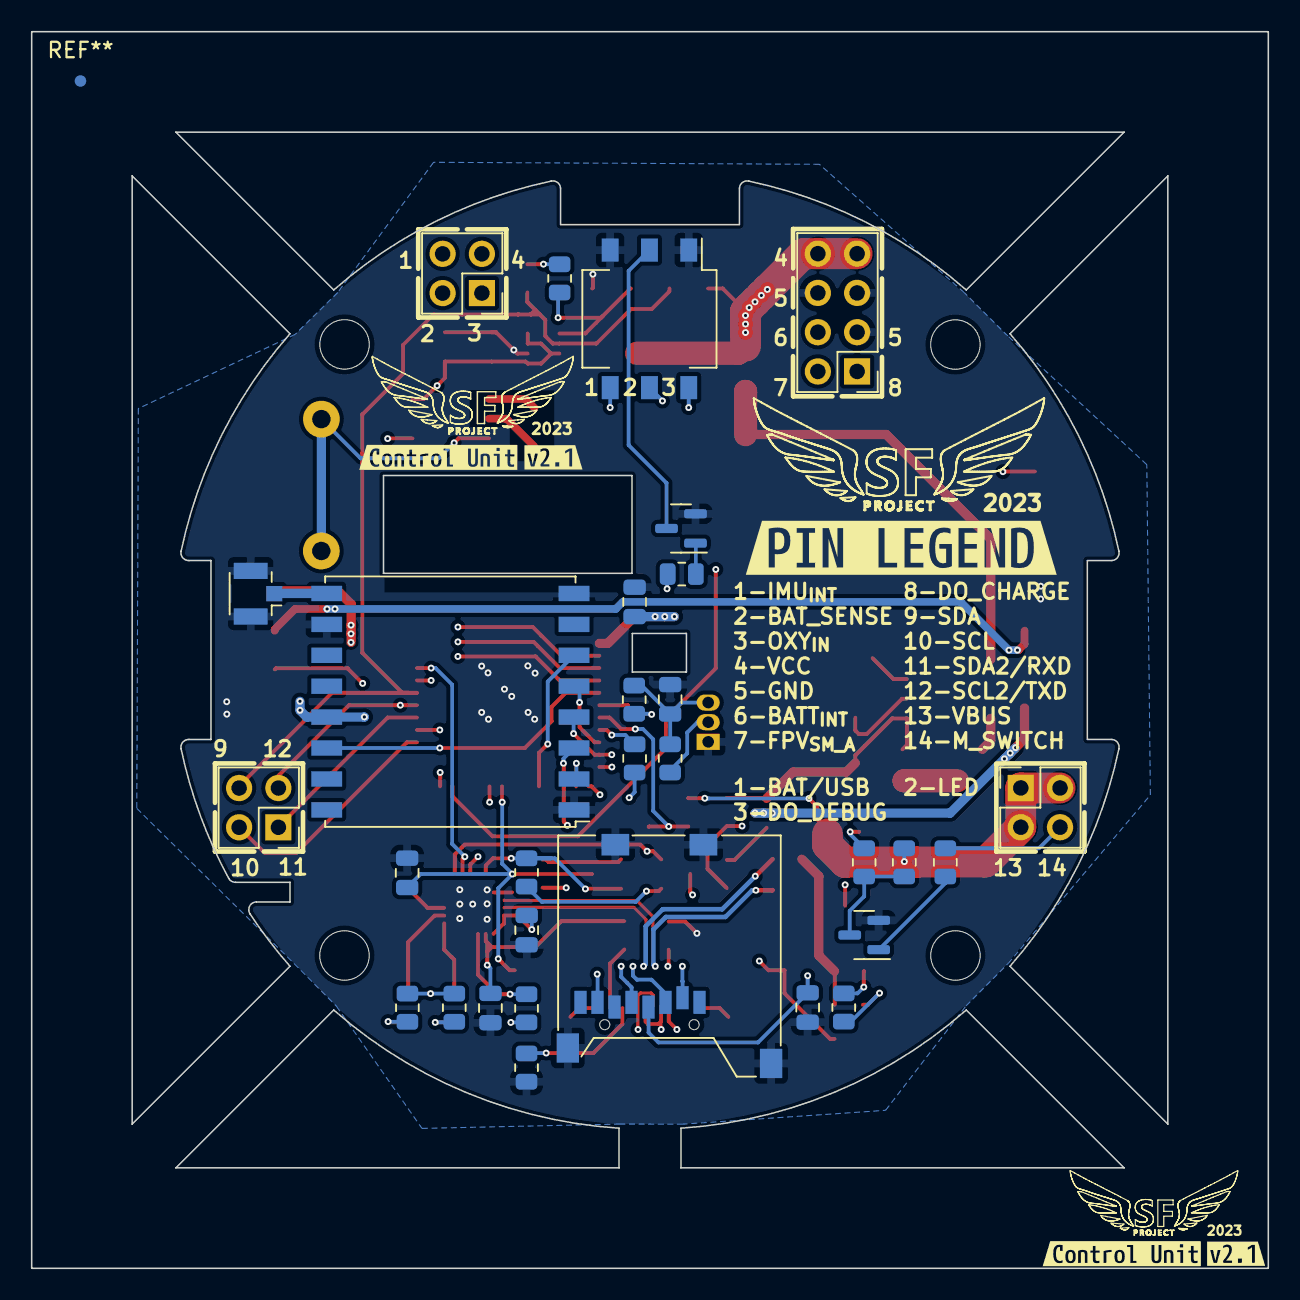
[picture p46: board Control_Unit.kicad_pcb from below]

Board: 4 copper layers, 80.0 x 80.0 mm, 95 parts (35 on the bottom side), 68 nets.

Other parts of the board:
kibuzzard-63BEB0CF, kibuzzard-63BEB0CF#2, kibuzzard-63BEB0CF#3, kibuzzard-63BEB0CF#4: G***; kibuzzard-63BEB0CF
kibuzzard-63BEB9E1: G***; kibuzzard-63BEB9E1
kibuzzard-644421C3: G***; kibuzzard-644421C3
kibuzzard-644421CD: G***; kibuzzard-644421CD
kibuzzard-644421E6: G***; kibuzzard-644421E6
kibuzzard-644422F5: G***; kibuzzard-644422F5

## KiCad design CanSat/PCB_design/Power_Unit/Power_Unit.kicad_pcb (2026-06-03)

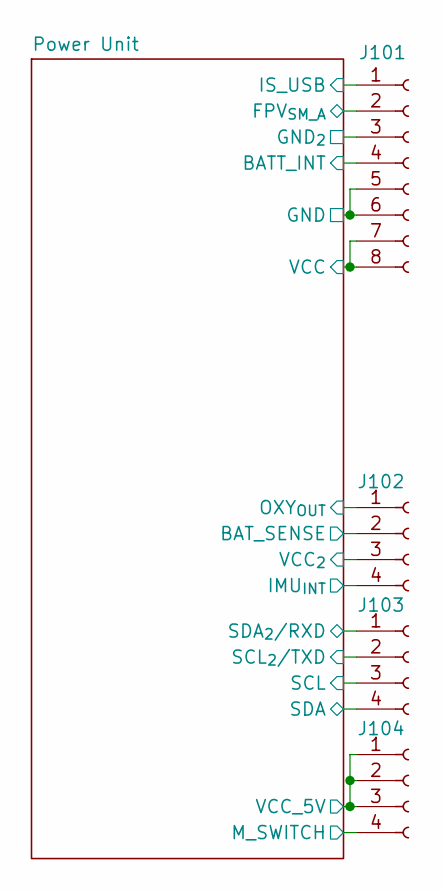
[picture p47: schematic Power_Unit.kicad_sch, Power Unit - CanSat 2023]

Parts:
J101: Conn_02x04_Female; PinSocket_2x04_P2.54mm_Vertical
J102, J103, J104: Conn_02x02_Female; PinSocket_2x02_P2.54mm_Vertical

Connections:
/Power Unit/BATT_INT: J101.4; also elsewhere on the board
/Power Unit/BAT_SENSE: J102.2; also elsewhere on the board
/Power Unit/FPV_{SM_A}: J101.2; also elsewhere on the board
/Power Unit/GND: J101.3, J101.5, J101.6; also elsewhere on the board
/Power Unit/IMU_{INT}: J102.4; also elsewhere on the board
/Power Unit/IS_USB: J101.1; also elsewhere on the board
/Power Unit/M_SWITCH: J104.4; also elsewhere on the board
/Power Unit/OXY_{OUT}: J102.1; also elsewhere on the board
/Power Unit/SCL: J103.3; also elsewhere on the board
/Power Unit/SCL_{2}/TXD: J103.2; also elsewhere on the board
/Power Unit/SDA: J103.4; also elsewhere on the board
/Power Unit/SDA_{2}/RXD: J103.1; also elsewhere on the board
/Power Unit/VCC: J101.7, J101.8, J102.3; also elsewhere on the board
/Power Unit/VCC_5V: J104.1, J104.2, J104.3; also elsewhere on the board

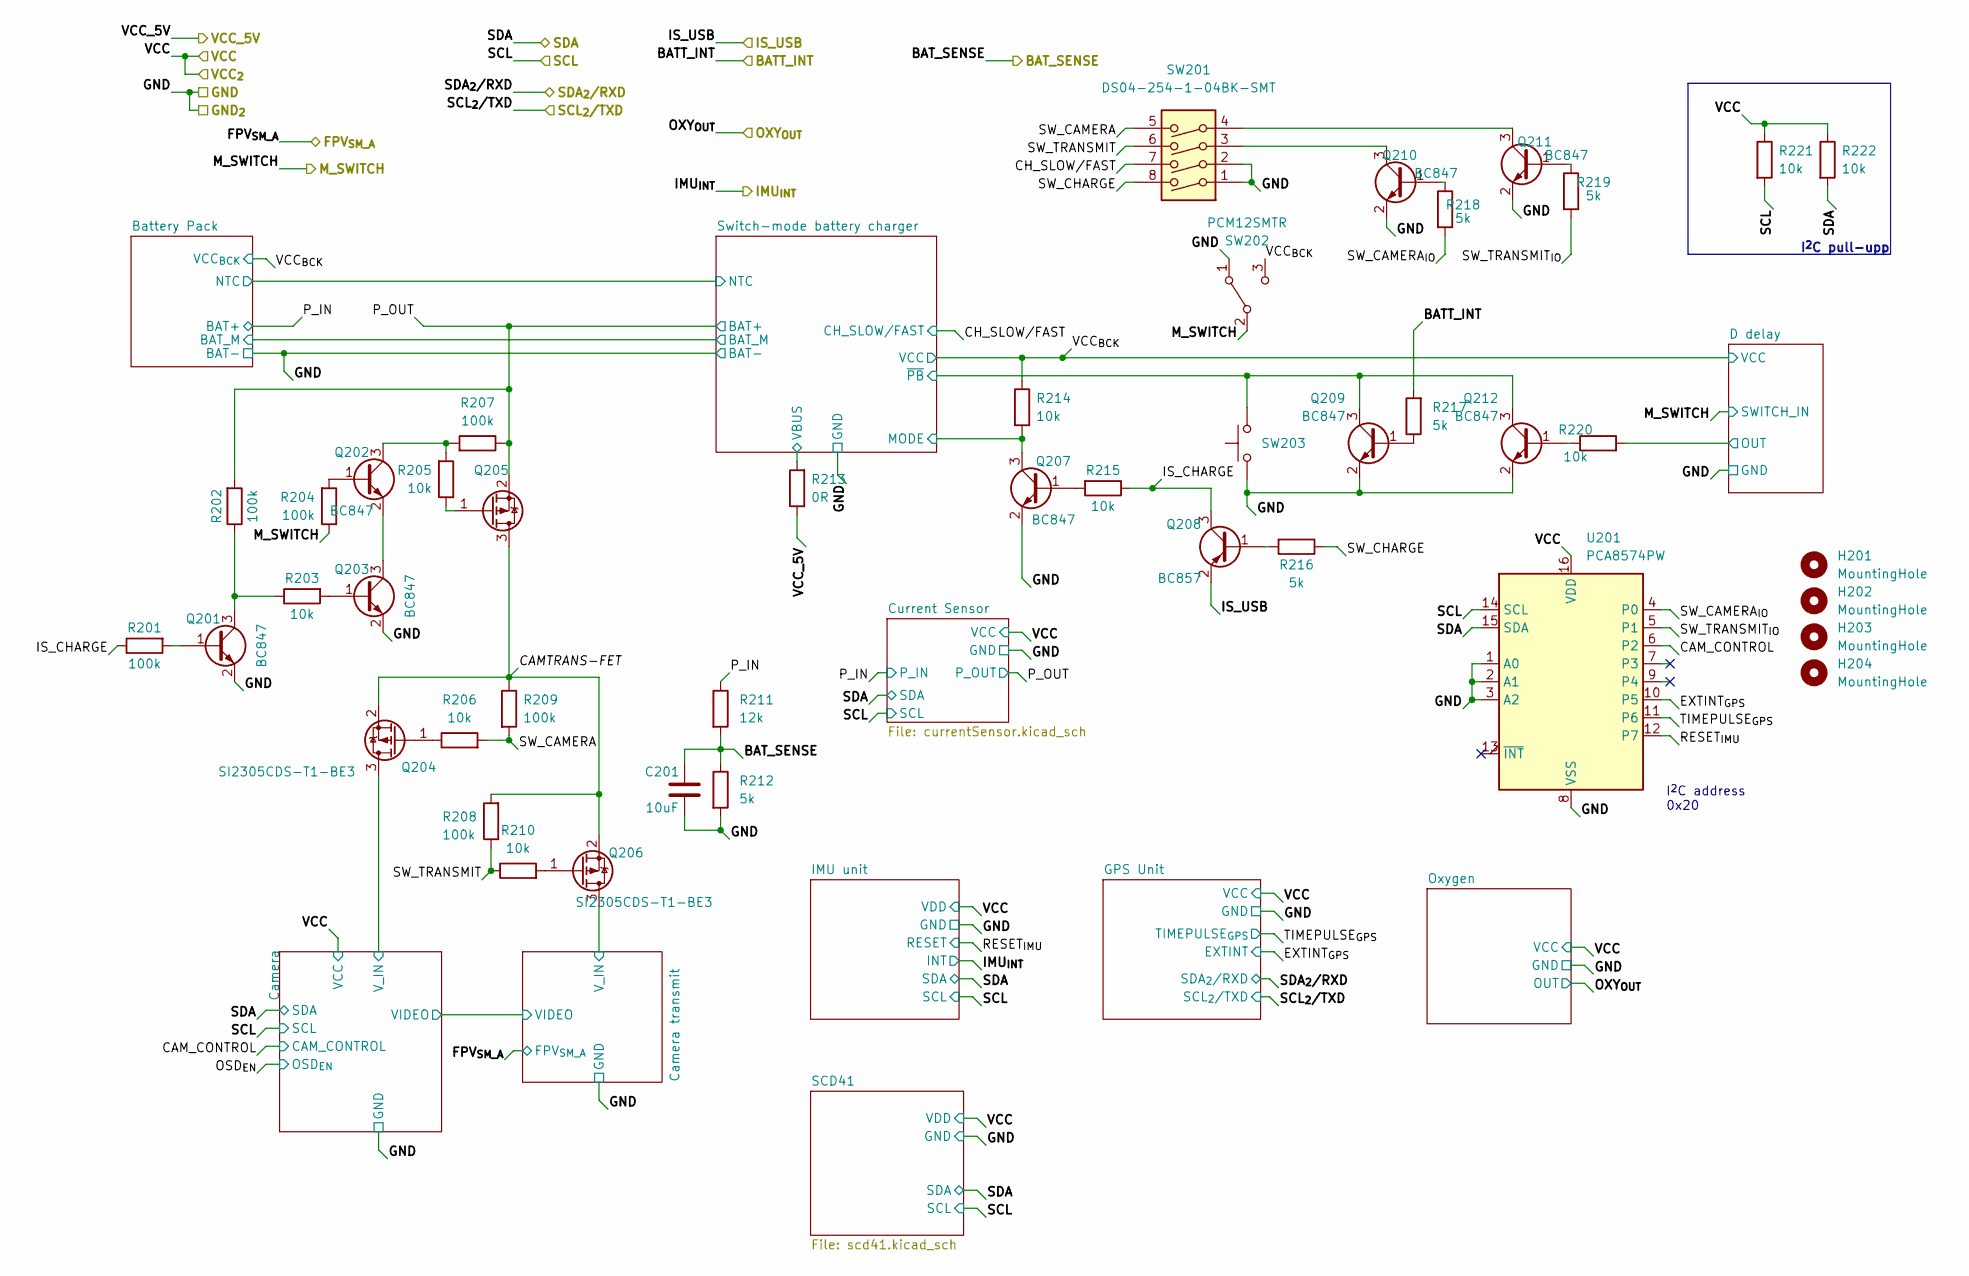
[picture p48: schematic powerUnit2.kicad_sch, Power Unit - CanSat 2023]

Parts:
C201: 10uF; C_0805_2012Metric
H201, H202, H203, H204: MountingHole; MountingHole_3.2mm_M3
Q201, Q202, Q203, Q207, Q209, Q210, Q211, Q212: BC847; SOT-23
Q204, Q205, Q206: SI2305CDS-T1-BE3; SOT-23
Q208: BC857; SOT-23
R201, R202, R204, R207, R208, R209: 100k; R_0805_2012Metric
R203, R205, R206, R210, R214, R215, R220, R221, R222: 10k; R_0805_2012Metric
R211: 12k; R_0805_2012Metric
R212, R216, R217, R218, R219: 5k; R_0805_2012Metric
R213: 0R; R_1206_3216Metric
SW201: DS04-254-1-04BK-SMT; SW_DIP_SPSTx04_Slide_Omron_A6S-410x_W8.9mm_P2.54mm
SW202: PCM12SMTR
SW203: LaskaKit tlačítko; Tlačítko SMD LaskaKit
U201: PCA8574PW; SOP65P640X110-16N

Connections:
/Power Unit/BATT_INT: R217.2; also elsewhere on the board
/Power Unit/BAT_SENSE: C201.1, R211.2, R212.1; also elsewhere on the board
/Power Unit/CAMTRANS-FET: Q204.2 (S), Q205.3 (D), Q206.2 (S), R208.2, R209.1
/Power Unit/CAM_CONTROL: U201.6 (P2); also elsewhere on the board
/Power Unit/CH_SLOW/FAST: SW201.7; also elsewhere on the board
/Power Unit/Camera transmit/V_IN: Q206.3 (D); also elsewhere on the board
/Power Unit/Camera/V_IN: Q204.3 (D); also elsewhere on the board
/Power Unit/D delay/OUT: R220.2; also elsewhere on the board
/Power Unit/EXTINT_{GPS}: U201.10 (P5); also elsewhere on the board
/Power Unit/GND: C201.2, Q201.2 (E), Q203.2 (E), Q207.2 (E), Q209.2 (E), Q210.2 (E), Q211.2 (E), Q212.2 (E), R212.2, SW201.1, SW201.2, SW202.1 (A), SW203.1, U201.1 (A0), U201.2 (A1), U201.3 (A2), U201.8 (VSS); also elsewhere on the board
/Power Unit/IS_CHARGE: Q208.3 (C), R201.1, R215.1
/Power Unit/IS_USB: Q208.2 (E); also elsewhere on the board
/Power Unit/M_SWITCH: R204.1, SW202.2 (B); also elsewhere on the board
/Power Unit/P_IN: R211.1; also elsewhere on the board
/Power Unit/P_OUT: Q205.2 (S), R202.2, R207.1; also elsewhere on the board
/Power Unit/RESET_{IMU}: U201.12 (P7); also elsewhere on the board
/Power Unit/SCL: R221.2, U201.14 (SCL); also elsewhere on the board
/Power Unit/SDA: R222.2, U201.15 (SDA); also elsewhere on the board
/Power Unit/SW_CAMERA: R206.2, R209.2, SW201.5
/Power Unit/SW_CAMERA_{IO}: R218.2, U201.4 (P0)
/Power Unit/SW_CHARGE: R216.1, SW201.8
/Power Unit/SW_TRANSMIT: R208.1, R210.1, SW201.6
/Power Unit/SW_TRANSMIT_{IO}: R219.2, U201.5 (P1)
/Power Unit/Switch-mode battery charger/MODE: Q207.3 (C), R214.2; also elsewhere on the board
/Power Unit/Switch-mode battery charger/VL: R213.2; also elsewhere on the board
/Power Unit/Switch-mode battery charger/~PB: Q209.3 (C), Q212.3 (C), SW203.2; also elsewhere on the board
/Power Unit/TIMEPULSE_{GPS}: U201.11 (P6); also elsewhere on the board
/Power Unit/VCC: R221.1, R222.1, U201.16 (VDD); also elsewhere on the board
/Power Unit/VCC_5V: R213.1; also elsewhere on the board
/Power Unit/VCC_{BCK}: R214.1, SW202.3 (C); also elsewhere on the board
unnamed: Q201.1 (B), R201.2
unnamed: Q201.3 (C), R202.1, R203.1
unnamed: Q202.1 (B), R204.2
unnamed: Q202.2 (E), Q203.3 (C)
unnamed: Q202.3 (C), R205.2, R207.2
unnamed: Q203.1 (B), R203.2
unnamed: Q204.1 (G), R206.1
unnamed: Q205.1 (G), R205.1
unnamed: Q206.1 (G), R210.2
unnamed: Q207.1 (B), R215.2
unnamed: Q208.1 (B), R216.2
unnamed: Q209.1 (B), R217.1
unnamed: Q210.1 (B), R218.1
unnamed: Q210.3 (C), SW201.3
unnamed: Q211.1 (B), R219.1
unnamed: Q211.3 (C), SW201.4
unnamed: Q212.1 (B), R220.1

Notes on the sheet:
I^{2}C address 0x20
I^{2}C pull-upp

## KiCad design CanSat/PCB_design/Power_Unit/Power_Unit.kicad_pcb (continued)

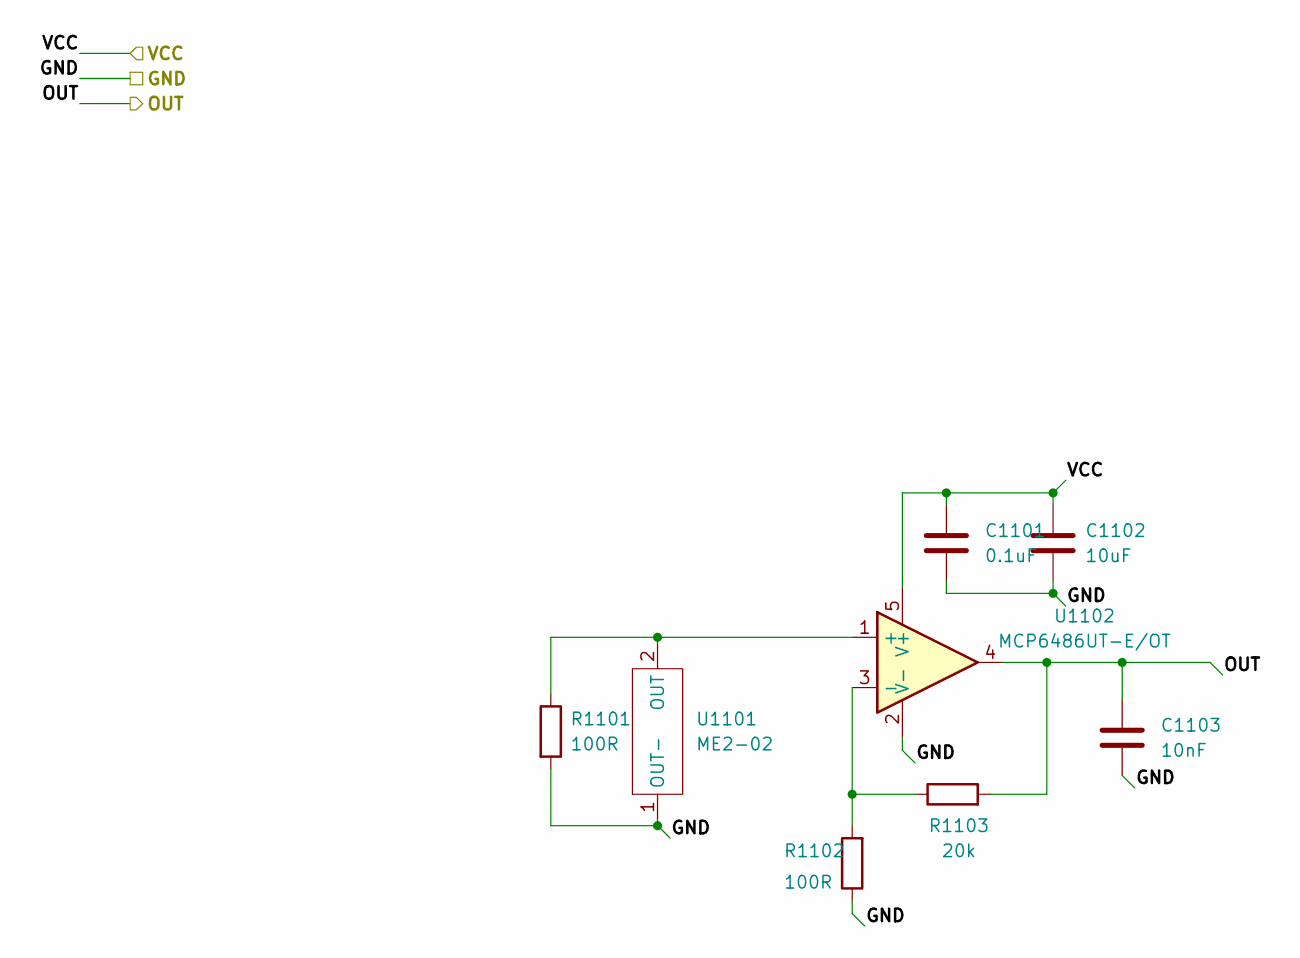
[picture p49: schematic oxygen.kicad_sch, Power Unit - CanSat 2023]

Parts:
C1101: 0.1uF; C_0805_2012Metric
C1102: 10uF; C_0805_2012Metric
C1103: 10nF; C_0805_2012Metric
R1101, R1102: 100R; R_0805_2012Metric
R1103: 20k; R_0805_2012Metric
U1101: ME2-02; ME2-O2
U1102: MCP6486UT-E/OT; SOT-23-5

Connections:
/Power Unit/GND: C1101.2, C1102.2, C1103.2, R1101.2, R1102.1, U1101.1 (OUT-), U1102.2 (V-); also elsewhere on the board
/Power Unit/OXY_{OUT}: C1103.1, R1103.2, U1102.4; also elsewhere on the board
/Power Unit/VCC: C1101.1, C1102.1, U1102.5 (V+); also elsewhere on the board
unnamed: R1101.1, U1101.2 (OUT), U1102.1 (+)
unnamed: R1102.2, R1103.1, U1102.3 (-)


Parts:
C801: 120nF; C_0805_2012Metric
C802: 6.8nF; C_0805_2012Metric
C803, C804: 0.1uF; C_0805_2012Metric
R801, R802: 10k; R_0805_2012Metric
U801: BNO055; LGA-28_5.2x3.8mm_P0.5mm

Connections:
/Power Unit/GND: C801.2, C802.2, C803.2, C804.2, U801.2 (GND), U801.5 (PS1), U801.6 (PS0), U801.15 (GNDIO), U801.16 (GNDIO), U801.17 (COM3), U801.18 (COM2), U801.25 (GNDIO); also elsewhere on the board
/Power Unit/IMU_{INT}: U801.14 (INT); also elsewhere on the board
/Power Unit/RESET_{IMU}: R802.2, U801.11 (~RESET); also elsewhere on the board
/Power Unit/SCL: U801.19 (COM1); also elsewhere on the board
/Power Unit/SDA: U801.20 (COM0); also elsewhere on the board
/Power Unit/VCC: C801.1, C802.1, C803.1, R801.2, R802.1, U801.3 (VDD), U801.28 (VDDIO); also elsewhere on the board
unnamed: C804.1, U801.9 (CAP)
unnamed: R801.1, U801.4 (~BOOT_LOAD_PIN)

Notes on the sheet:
Address select LOW 0x28 HIGH 0x29


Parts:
AE1001: Antenna_Shield; U.FL_Hirose_U.FL-R-SMT-1_Vertical
BT1001: Backup battery; 2989
C1001: 1uF; C_0805_2012Metric
C1002: 0.1uF; C_0805_2012Metric
D1001: APT2012LSECK/J4-PRV; LED_0805_2012Metric
D1002: ESD7351HT1G; D_SOD-323
JP1001, JP1002: SolderJumper_3_Bridged12; SolderJumper-3_P1.3mm_Bridged12_Pad1.0x1.5mm
L1001: 27nH; L_0805_2012Metric
Q1001: BC847; SOT-23
R1001: 5k; R_0805_2012Metric
R1002: 750R; R_0805_2012Metric
R1003: 10R; R_0805_2012Metric
U1001: NEO-M9N; ublox_NEO
U1002, U1003: TS5A3159DBV; SOT-23-6

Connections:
/Power Unit/EXTINT_{GPS}: U1001.4 (EXTINT); also elsewhere on the board
/Power Unit/GND: AE1001.2 (Shield), BT1001.2 (-), C1001.1, C1002.1, D1002.2 (A), Q1001.2 (E), U1001.7 (VDD_USB), U1001.10 (GND), U1002.2 (GND), U1003.2 (GND); also elsewhere on the board
/Power Unit/SCL_{2}/TXD: U1003.1; also elsewhere on the board
/Power Unit/SDA_{2}/RXD: U1002.1; also elsewhere on the board
/Power Unit/TIMEPULSE_{GPS}: R1001.1, U1001.3 (TIMEPULSE); also elsewhere on the board
/Power Unit/VCC: C1001.2, D1001.2 (A), U1001.23 (VCC), U1002.5 (V+), U1002.6, U1003.5 (V+), U1003.6; also elsewhere on the board
unnamed: AE1001.1 (A), D1002.1 (K), L1001.2, U1001.11 (RF_IN)
unnamed: BT1001.1 (+), U1001.22 (V_BCKP)
unnamed: C1002.2, L1001.1, R1003.1
unnamed: D1001.1 (K), R1002.1
unnamed: JP1001.1 (A), U1001.18 (SDA/~SPI_CS)
unnamed: JP1001.2 (C), U1002.4
unnamed: JP1001.3 (B), U1001.20 (TXD/SPI_MISO)
unnamed: JP1002.1 (A), U1001.19 (SCL/SPI_CLK)
unnamed: JP1002.2 (C), U1003.4
unnamed: JP1002.3 (B), U1001.21 (RXD/SPI_MOSI)
unnamed: Q1001.1 (B), R1001.2
unnamed: Q1001.3 (C), R1002.2
unnamed: R1003.2, U1001.9 (VCC_RF)

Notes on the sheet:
ESD protection
I2C isolation


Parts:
C401: 10uF; C_0805_2012Metric
R401: PE1206FRE470R04L; R_1206_Current
U401: INA219AxD; SOIC-8_3.9x4.9mm_P1.27mm

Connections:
/Power Unit/GND: C401.1, U401.6 (GND); also elsewhere on the board
/Power Unit/P_IN: R401.1, U401.8 (IN+); also elsewhere on the board
/Power Unit/P_OUT: R401.2, U401.7 (IN-); also elsewhere on the board
/Power Unit/SCL: U401.4 (SCL); also elsewhere on the board
/Power Unit/SDA: U401.3 (SDA); also elsewhere on the board
/Power Unit/VCC: C401.2, U401.1 (A1), U401.2 (A0), U401.5 (VS); also elsewhere on the board

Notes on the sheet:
I^{2}C address 0x45


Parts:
C701, C702, C707: 22uF; C_0805_2012Metric
C703, C706: 1uF; C_0805_2012Metric
C704, C705: 0.1uF; C_0805_2012Metric
C708: 4.7uF; C_0805_2012Metric
D701: B330A; D_SMA
D702, D703, D704, D705: APT2012LZGCK; LED_0805_2012Metric
D706: APT2012LSECK/J3-PRV; LED_0805_2012Metric
L701: SRP7050AA-2R2M; L_Bourns_SRP7050AA
R701: 0R5; R_0805_2012Metric
R702: 3k16; R_0805_2012Metric
R703, R716, R718: 10k; R_0805_2012Metric
R704: 1k87; R_0805_2012Metric
R705: 1k3; R_0805_2012Metric
R706: 5k11; R_0805_2012Metric
R707, R708, R709, R710: 910R; R_0805_2012Metric
R712: 143k; R_0805_2012Metric
R713: 82k; R_0805_2012Metric
R714: 820k; R_0805_2012Metric
R715: 75k; R_0805_2012Metric
R717: 27k4; R_0805_2012Metric
U701, U703: TS5A3159DBV; SOT-23-6
U702: MP2639AGR-Z; MP2639AGRZ; Mouser Part Number 946-MP2639AGR-Z

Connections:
/Power Unit/Battery Pack/BAT_M: R701.2; also elsewhere on the board
/Power Unit/Battery Pack/NTC: R704.1, R706.1, U702.20 (NTC); also elsewhere on the board
/Power Unit/CH_SLOW/FAST: R716.2, U703.6; also elsewhere on the board
/Power Unit/GND: C701.2, C702.2, C703.2, C705.2, C706.2, C707.2, C708.2, D701.2 (A), R702.2, R706.2, R712.2, R713.2, R714.2, R715.2, R718.2, U701.1, U701.2 (GND), U702.5 (PGND), U702.10 (AGND), U703.2 (GND); also elsewhere on the board
/Power Unit/P_OUT: C701.1, C702.1, C703.1, U702.3 (VH); also elsewhere on the board
/Power Unit/Switch-mode battery charger/BST: C704.2, U702.6 (BST)
/Power Unit/Switch-mode battery charger/FB: R702.1, R703.2, U702.17 (FB)
/Power Unit/Switch-mode battery charger/IB: U702.21 (IB)
/Power Unit/Switch-mode battery charger/ILIM: U702.24 (ILIM), U703.4
/Power Unit/Switch-mode battery charger/ISET: R712.1, U702.23 (ISET)
/Power Unit/Switch-mode battery charger/LX: D701.1 (K), L701.2, U702.2 (LX)
/Power Unit/Switch-mode battery charger/MODE: U701.6, U702.8 (MODE); also elsewhere on the board
/Power Unit/Switch-mode battery charger/OLIM: R715.1, U702.22 (OLIM)
/Power Unit/Switch-mode battery charger/SW: C704.1, L701.1, U702.4 (SW)
/Power Unit/Switch-mode battery charger/TMR: C705.1, U702.11 (TMR)
/Power Unit/Switch-mode battery charger/VL: C707.1, C708.1, R703.1, R717.1, U702.1 (VL); also elsewhere on the board
/Power Unit/Switch-mode battery charger/VLIM: R717.2, R718.1, U702.18 (VLIM)
/Power Unit/Switch-mode battery charger/VNTC: D706.2 (A), R704.2, R707.1, R708.1, R709.1, R710.1, U702.19 (VNTC)
/Power Unit/Switch-mode battery charger/~ACLK: U702.25 (~ACLK)
/Power Unit/Switch-mode battery charger/~CHG: R705.2, U702.26 (~CHG)
/Power Unit/Switch-mode battery charger/~PB: U702.7 (~PB); also elsewhere on the board
/Power Unit/VCC_{BCK}: C706.1, R716.1, U701.5 (V+), U702.9 (VCC), U703.5 (V+); also elsewhere on the board
unnamed: D702.1 (K), U702.13 (LED1)
unnamed: D702.2 (A), R710.2
unnamed: D703.1 (K), U702.14 (LED2)
unnamed: D703.2 (A), R707.2
unnamed: D704.1 (K), U702.15 (LED3)
unnamed: D704.2 (A), R708.2
unnamed: D705.1 (K), U702.16 (LED4)
unnamed: D705.2 (A), R709.2
unnamed: D706.1 (K), R705.1
unnamed: R701.1, U701.3
unnamed: R713.1, U703.3
unnamed: R714.1, U703.1
unnamed: U701.4, U702.12 (MIND)

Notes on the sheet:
5.38V
75k 2.84A
E48 1k87
Battery
Current limit 260mA -> 820k 2.6A -> 82k
SRP7050AA-2R2M
NRBE104J3435B2J Cold = 0°C = 27k74 Cool = 5°C Warm = 50°C Hot = 65°C = 2k5869
143k 1.5A
E48 5k11


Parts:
C901: 0.1uF; C_0805_2012Metric
U901: SCD41; XDCR_SCD41-D-R2

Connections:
/Power Unit/GND: C901.2, U901.6 (GND), U901.20 (GND), U901.21 (GND); also elsewhere on the board
/Power Unit/SCL: U901.9 (SCL); also elsewhere on the board
/Power Unit/SDA: U901.10 (SDA); also elsewhere on the board
/Power Unit/VCC: C901.1, U901.7 (VDD), U901.19 (VDDH); also elsewhere on the board

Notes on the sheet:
I^{2}C address 0x62

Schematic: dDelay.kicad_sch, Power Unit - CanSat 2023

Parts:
C1201, C1202: 22uF; C_0805_2012Metric
C1203: NC; C_0805_2012Metric
C1204: 10uF; C_0805_2012Metric
Q1201, Q1203, Q1204, Q1206: BC857; SOT-23
Q1202, Q1205: BC847; SOT-23
R1201, R1202, R1203, R1204, R1205, R1206, R1209: 100k; R_0805_2012Metric
R1207: 10k; R_0805_2012Metric
R1208: 15k; R_0805_2012Metric

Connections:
/Power Unit/D delay/OUT: R1207.2, R1208.2, R1209.2; also elsewhere on the board
/Power Unit/GND: Q1202.2 (E), Q1205.2 (E), R1209.1; also elsewhere on the board
/Power Unit/M_SWITCH: R1201.1, R1202.1, R1205.1, R1206.1; also elsewhere on the board
/Power Unit/VCC_{BCK}: Q1201.2 (E), Q1204.2 (E); also elsewhere on the board
unnamed: C1201.1, C1202.1, Q1201.3 (C), Q1203.2 (E)
unnamed: C1201.2, C1202.2, Q1203.3 (C), R1208.1
unnamed: C1203.1, C1204.1, Q1204.3 (C), Q1206.2 (E)
unnamed: C1203.2, C1204.2, Q1206.3 (C), R1207.1
unnamed: Q1201.1 (B), R1201.2
unnamed: Q1202.1 (B), R1202.2
unnamed: Q1202.3 (C), R1203.1
unnamed: Q1203.1 (B), R1203.2
unnamed: Q1204.1 (B), R1204.2
unnamed: Q1205.1 (B), R1205.2
unnamed: Q1205.3 (C), R1204.1
unnamed: Q1206.1 (B), R1206.2

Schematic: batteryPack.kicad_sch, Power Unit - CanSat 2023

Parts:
BT301, BT302: Battery_Cell; JST_PH_B2B-PH-K_1x02_P2.00mm_Vertical
C301, C302: 22uF; C_0805_2012Metric
Q301, Q302: BC847; SOT-23
R301, R304: 10k; R_0805_2012Metric
R302, R303: 220k; R_0805_2012Metric
TH301, TH302: NRBE104J3435B2J; Molex_PicoBlade_53047-0210_1x02_P1.25mm_Vertical
U301: TS5A3159DBV; SOT-23-6

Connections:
/Power Unit/Battery Pack/BAT_M: BT301.2 (-), BT302.1 (+); also elsewhere on the board
/Power Unit/Battery Pack/NTC: U301.4; also elsewhere on the board
/Power Unit/Battery Pack/NTC_SWITCH: C301.1, Q301.3 (C), R301.1, U301.6
/Power Unit/GND: BT302.2 (-), Q301.2 (E), Q302.2 (E), TH301.2, TH302.2, U301.2 (GND); also elsewhere on the board
/Power Unit/P_IN: BT301.1 (+); also elsewhere on the board
/Power Unit/VCC_{BCK}: R301.2, R302.2, R303.2, R304.2, U301.5 (V+); also elsewhere on the board
unnamed: C301.2, Q302.1 (B), R302.1
unnamed: C302.1, Q301.1 (B), R303.1
unnamed: C302.2, Q302.3 (C), R304.1
unnamed: TH301.1, U301.1
unnamed: TH302.1, U301.3

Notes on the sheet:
BATTERY PACK
NRBE104J3435B2J Cold = -5 = 34k64 Cool = 5 Warm = 50 Hot = 65 = 2k5869

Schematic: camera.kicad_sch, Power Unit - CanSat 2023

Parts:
J501: Conn_01x02; Molex_PicoBlade_53261-0271_1x02-1MP_P1.25mm_Horizontal
J502: Conn_01x03; Molex_PicoBlade_53047-0310_1x03_P1.25mm_Vertical
J503, J504: Conn_01x02; Molex_PicoBlade_53047-0210_1x02_P1.25mm_Vertical
Q501: BC847; SOT-23
R501: 5k; R_0805_2012Metric
U501: AD5246BKSZ100; SOT65P210X110-6N

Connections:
/Power Unit/CAM_CONTROL: R501.1; also elsewhere on the board
/Power Unit/Camera transmit/VIDEO: J501.1, J502.1; also elsewhere on the board
/Power Unit/Camera/V_IN: J502.3; also elsewhere on the board
/Power Unit/GND: J501.2, J502.2, U501.2 (VSS); also elsewhere on the board
/Power Unit/SCL: U501.3 (SCL); also elsewhere on the board
/Power Unit/SDA: U501.4 (SDA); also elsewhere on the board
/Power Unit/VCC: U501.1 (VDD); also elsewhere on the board
unnamed: J503.1, Q501.2 (E)
unnamed: J503.2, Q501.3 (C)
unnamed: J504.1, U501.5 (B)
unnamed: J504.2, U501.6 (W)
unnamed: Q501.1 (B), R501.2

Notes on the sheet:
I^{2}C address W - 0x5C R - 0x5D

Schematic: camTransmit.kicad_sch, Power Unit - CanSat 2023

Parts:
U601: TBS_UNIFY_PRO32_5G8_nano; TBS UNIFY PRO32 5G8 nano

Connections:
/Power Unit/Camera transmit/VIDEO: U601.5 (Video); also elsewhere on the board
/Power Unit/Camera transmit/V_IN: U601.1 (V_{IN}); also elsewhere on the board
/Power Unit/FPV_{SM_A}: U601.6 (SA); also elsewhere on the board
/Power Unit/GND: U601.2 (GND), U601.4 (GND); also elsewhere on the board

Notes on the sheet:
https://www.fyft.cz/tbs-unify-pro32-nano-5g8/



Board: 4 copper layers, 60.7 x 61.3 mm, 162 parts (63 on the bottom side), 119 nets.

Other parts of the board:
kibuzzard-63BEDE70, kibuzzard-63BEDE70#2: G***; kibuzzard-63BEDE70
kibuzzard-642811A6: G***; kibuzzard-642811A6
kibuzzard-642811B8: G***; kibuzzard-642811B8

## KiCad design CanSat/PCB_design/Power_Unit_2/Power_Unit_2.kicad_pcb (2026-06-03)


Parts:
J101: Conn_02x04_Female; PinSocket_2x04_P2.54mm_Vertical
J102, J103, J104: Conn_02x02_Female; PinSocket_2x02_P2.54mm_Vertical

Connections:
/Power Unit/BATT_INT: J101.4
/Power Unit/BAT_SENSE: J102.2; also elsewhere on the board
/Power Unit/FPV_{SM_A}: J101.2; also elsewhere on the board
/Power Unit/GND: J101.3, J101.5, J101.6; also elsewhere on the board
/Power Unit/IMU_{INT}: J102.4; also elsewhere on the board
/Power Unit/IS_USB: J101.1
/Power Unit/M_SWITCH: J104.4; also elsewhere on the board
/Power Unit/OXY_{OUT}: J102.1; also elsewhere on the board
/Power Unit/SCL: J103.3; also elsewhere on the board
/Power Unit/SCL_{2}/TXD: J103.2; also elsewhere on the board
/Power Unit/SDA: J103.4; also elsewhere on the board
/Power Unit/SDA_{2}/RXD: J103.1; also elsewhere on the board
/Power Unit/VCC: J101.7, J101.8, J102.3; also elsewhere on the board
/Power Unit/VCC_5V: J104.1, J104.2, J104.3; also elsewhere on the board


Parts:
BT201, BT202: Battery_Cell; JST_PH_B2B-PH-K_1x02_P2.00mm_Vertical
C201: 10uF; C_0805_2012Metric
H201, H202, H203, H204: MountingHole; MountingHole_3.2mm_M3
J201: Conn_01x03; JST_PH_S3B-PH-SM4-TB_1x03-1MP_P2.00mm_Horizontal
Q201, Q202, Q204, Q205, Q206: SI2305CDS-T1-BE3; SOT-23
Q203, Q207, Q208: BC847; SOT-23
R201, R202, R207, R210, R213, R218, R219: 10k; R_0805_2012Metric
R203, R204, R205, R206, R211, R212: 100k; R_0805_2012Metric
R208: 12k; R_0805_2012Metric
R209, R216, R217: 5k; R_0805_2012Metric
R214: 0R; R_0805_2012Metric
R215: 0R; R_1206_3216Metric
SW201: DS04-254-1-04BK-SMT; SW_DIP_SPSTx04_Slide_Omron_A6S-410x_W8.9mm_P2.54mm
SW202: PCM12SMTR
U201: PCA8574PW; SOP65P640X110-16N

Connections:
/Power Unit/BATT: BT201.1 (+), Q201.3 (D), Q204.2 (S), R203.2, R206.2, SW202.3 (C)
/Power Unit/BAT_SENSE: C201.1, R208.2, R209.1; also elsewhere on the board
/Power Unit/CAMTRANS-FET: Q205.2 (S), Q206.2 (S), R211.2, R212.1; also elsewhere on the board
/Power Unit/CAM_CONTROL: U201.6 (P2); also elsewhere on the board
/Power Unit/Camera transmit/V_IN: Q206.3 (D); also elsewhere on the board
/Power Unit/Camera/V_IN: Q205.3 (D); also elsewhere on the board
/Power Unit/Current Sensor/P_IN: Q204.3 (D), R208.1; also elsewhere on the board
/Power Unit/EXTINT_{GPS}: U201.10 (P5); also elsewhere on the board
/Power Unit/GND: BT202.2 (-), C201.2, J201.3, Q203.2 (E), Q207.2 (E), Q208.2 (E), R209.2, R214.2, SW201.3, SW201.4, SW202.1 (A), U201.1 (A0), U201.2 (A1), U201.3 (A2), U201.8 (VSS); also elsewhere on the board
/Power Unit/GPI_{0}: SW201.6, U201.7 (P3)
/Power Unit/GPI_{1}: SW201.5, U201.9 (P4)
/Power Unit/M_SWITCH: R201.1, R202.1, R203.1, R204.1, R205.1, SW202.2 (B); also elsewhere on the board
/Power Unit/RESET_{IMU}: U201.12 (P7); also elsewhere on the board
/Power Unit/SCL: R218.2, U201.14 (SCL); also elsewhere on the board
/Power Unit/SDA: R219.2, U201.15 (SDA); also elsewhere on the board
/Power Unit/SW_CAMERA: R210.2, R212.2, SW201.8
/Power Unit/SW_CAMERA_{IO}: R217.2, U201.5 (P1)
/Power Unit/SW_TRANSMIT: R211.1, R213.1, SW201.7
/Power Unit/SW_TRANSMIT_{IO}: R216.2, U201.4 (P0)
/Power Unit/Step-down/GND: R214.1; also elsewhere on the board
/Power Unit/Step-down/VCC_5V: R215.2; also elsewhere on the board
/Power Unit/TIMEPULSE_{GPS}: U201.11 (P6); also elsewhere on the board
/Power Unit/VCC: R218.1, R219.1, U201.16 (VDD); also elsewhere on the board
/Power Unit/VCC_5V: R215.1; also elsewhere on the board
unnamed: BT201.2 (-), BT202.1 (+), Q202.3 (D), R204.2
unnamed: J201.1, Q201.2 (S)
unnamed: J201.2, Q202.2 (S)
unnamed: Q201.1 (G), R201.2
unnamed: Q202.1 (G), R202.2
unnamed: Q203.1 (B), R205.2
unnamed: Q203.3 (C), R206.1, R207.2
unnamed: Q204.1 (G), R207.1
unnamed: Q205.1 (G), R210.1
unnamed: Q206.1 (G), R213.2
unnamed: Q207.1 (B), R216.1
unnamed: Q207.3 (C), SW201.2
unnamed: Q208.3 (C), SW201.1
unnamed: Q208.1 (B), R217.1

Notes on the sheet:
I^{2}C address 0x20
I^{2}C pull-upp

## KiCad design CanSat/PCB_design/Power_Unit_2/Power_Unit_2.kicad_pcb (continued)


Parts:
C301: 0.1uF; C_0805_2012Metric
C302, C303: TPSB686K010R0600; CP_EIA-3528-21_Kemet-B; Mouser Part Number 581-TPSB686K010R0600
C304: 0.47uF; C_0805_2012Metric
C305: 293D227X9010D2TE3; CP_EIA-7343-31_Kemet-D; Mouser Part Number 74-293D227X9010D2TE3
D301: B330A; D_SMA
IC301: MAX1626ESA+T; SOIC127P600X175-8N; Mouser Part Number 700-MAX1626ESAT
L301: CDRH125NP-220MC; CDRH125101MC; Mouser Part Number 851-CDRH125NP-220MC
Q301: SI2305CDS-T1-BE3; SOT-23
R301: PE1206FRE470R04L; R_1206_Current

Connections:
/Power Unit/CAMTRANS-FET: C302.1, C303.1, C304.1, IC301.2 (~_3/5), IC301.5 (V+), R301.1; also elsewhere on the board
/Power Unit/Step-down/GND: C301.2, C302.2, C303.2, C304.2, C305.2, D301.2 (A), IC301.3 (SHDN), IC301.8 (GND); also elsewhere on the board
/Power Unit/Step-down/L_MOSFET: IC301.6 (CS), Q301.2 (S), R301.2
/Power Unit/Step-down/L_{SWITCH}: D301.1 (K), L301.1, Q301.3 (D)
/Power Unit/Step-down/VCC_5V: C305.1, IC301.1 (OUT), L301.2; also elsewhere on the board
unnamed: C301.1, IC301.4 (REF)
unnamed: IC301.7 (EXT), Q301.1 (G)

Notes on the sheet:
STEP-DOWN


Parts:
U1001: TBS_UNIFY_PRO32_5G8_nano; TBS UNIFY PRO32 5G8 nano

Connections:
/Power Unit/Camera transmit/VIDEO: U1001.5 (Video); also elsewhere on the board
/Power Unit/Camera transmit/V_IN: U1001.1 (V_{IN}); also elsewhere on the board
/Power Unit/FPV_{SM_A}: U1001.6 (SA); also elsewhere on the board
/Power Unit/GND: U1001.2 (GND), U1001.4 (GND); also elsewhere on the board

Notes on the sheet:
https://www.fyft.cz/tbs-unify-pro32-nano-5g8/


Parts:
C401: 10uF; C_0805_2012Metric
R401: PE1206FRE470R04L; R_1206_Current
U401: INA219AxD; SOIC-8_3.9x4.9mm_P1.27mm

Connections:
/Power Unit/CAMTRANS-FET: R401.2, U401.7 (IN-); also elsewhere on the board
/Power Unit/Current Sensor/P_IN: R401.1, U401.8 (IN+); also elsewhere on the board
/Power Unit/GND: C401.1, U401.6 (GND); also elsewhere on the board
/Power Unit/SCL: U401.4 (SCL); also elsewhere on the board
/Power Unit/SDA: U401.3 (SDA); also elsewhere on the board
/Power Unit/VCC: C401.2, U401.1 (A1), U401.2 (A0), U401.5 (VS); also elsewhere on the board

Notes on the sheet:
I^{2}C address 0x45


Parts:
C701: 0.1uF; C_0805_2012Metric
U701: SCD41; XDCR_SCD41-D-R2

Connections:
/Power Unit/GND: C701.2, U701.6 (GND), U701.20 (GND), U701.21 (GND); also elsewhere on the board
/Power Unit/SCL: U701.9 (SCL); also elsewhere on the board
/Power Unit/SDA: U701.10 (SDA); also elsewhere on the board
/Power Unit/VCC: C701.1, U701.7 (VDD), U701.19 (VDDH); also elsewhere on the board

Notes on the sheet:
I^{2}C address 0x62


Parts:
C501: 120nF; C_0805_2012Metric
C502: 6.8nF; C_0805_2012Metric
C503, C504: 0.1uF; C_0805_2012Metric
R501, R502: 10k; R_0805_2012Metric
U501: BNO055; LGA-28_5.2x3.8mm_P0.5mm

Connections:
/Power Unit/GND: C501.2, C502.2, C503.2, C504.2, U501.2 (GND), U501.5 (PS1), U501.6 (PS0), U501.15 (GNDIO), U501.16 (GNDIO), U501.17 (COM3), U501.18 (COM2), U501.25 (GNDIO); also elsewhere on the board
/Power Unit/IMU_{INT}: U501.14 (INT); also elsewhere on the board
/Power Unit/RESET_{IMU}: R502.2, U501.11 (~RESET); also elsewhere on the board
/Power Unit/SCL: U501.19 (COM1); also elsewhere on the board
/Power Unit/SDA: U501.20 (COM0); also elsewhere on the board
/Power Unit/VCC: C501.1, C502.1, C503.1, R501.2, R502.1, U501.3 (VDD), U501.28 (VDDIO); also elsewhere on the board
unnamed: C504.1, U501.9 (CAP)
unnamed: R501.1, U501.4 (~BOOT_LOAD_PIN)

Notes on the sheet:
Address select LOW 0x28 HIGH 0x29


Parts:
AE601: Antenna_Shield; U.FL_Hirose_U.FL-R-SMT-1_Vertical
BT601: Backup battery; 2989
C601: 1uF; C_0805_2012Metric
C602: 0.1uF; C_0805_2012Metric
D601: APT2012LSECK/J4-PRV; LED_0805_2012Metric
D602: ESD7351HT1G; D_SOD-323
JP601, JP602: SolderJumper_3_Bridged12; SolderJumper-3_P1.3mm_Bridged12_Pad1.0x1.5mm
L601: 27nH; L_0805_2012Metric
Q601: BC847; SOT-23
R601: 5k; R_0805_2012Metric
R602: 750R; R_0805_2012Metric
R603: 10R; R_0805_2012Metric
U601, U602: TS5A3159DBV; SOT-23-6
U603: NEO-M9N; ublox_NEO

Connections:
/Power Unit/EXTINT_{GPS}: U603.4 (EXTINT); also elsewhere on the board
/Power Unit/GND: AE601.2 (Shield), BT601.2 (-), C601.1, C602.1, D602.2 (A), Q601.2 (E), U601.2 (GND), U602.2 (GND), U603.7 (VDD_USB), U603.10 (GND); also elsewhere on the board
/Power Unit/SCL_{2}/TXD: U602.1; also elsewhere on the board
/Power Unit/SDA_{2}/RXD: U601.1; also elsewhere on the board
/Power Unit/TIMEPULSE_{GPS}: R601.1, U603.3 (TIMEPULSE); also elsewhere on the board
/Power Unit/VCC: C601.2, D601.2 (A), U601.5 (V+), U601.6, U602.5 (V+), U602.6, U603.23 (VCC); also elsewhere on the board
unnamed: AE601.1 (A), D602.1 (K), L601.2, U603.11 (RF_IN)
unnamed: BT601.1 (+), U603.22 (V_BCKP)
unnamed: C602.2, L601.1, R603.1
unnamed: D601.1 (K), R602.1
unnamed: JP601.1 (A), U603.18 (SDA/~SPI_CS)
unnamed: JP601.2 (C), U601.4
unnamed: JP601.3 (B), U603.20 (TXD/SPI_MISO)
unnamed: JP602.1 (A), U603.19 (SCL/SPI_CLK)
unnamed: JP602.2 (C), U602.4
unnamed: JP602.3 (B), U603.21 (RXD/SPI_MOSI)
unnamed: Q601.1 (B), R601.2
unnamed: Q601.3 (C), R602.2
unnamed: R603.2, U603.9 (VCC_RF)

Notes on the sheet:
ESD protection
I2C isolation

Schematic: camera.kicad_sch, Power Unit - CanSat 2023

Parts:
J901: Conn_01x02; Molex_PicoBlade_53261-0271_1x02-1MP_P1.25mm_Horizontal
J902: Conn_01x03; Molex_PicoBlade_53047-0310_1x03_P1.25mm_Vertical
J903, J904: Conn_01x02; Molex_PicoBlade_53047-0210_1x02_P1.25mm_Vertical
Q901: BC857; SOT-23
R901: 5k; R_0805_2012Metric
U901: AD5246BKSZ100; SOT65P210X110-6N

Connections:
/Power Unit/CAM_CONTROL: R901.1; also elsewhere on the board
/Power Unit/Camera transmit/VIDEO: J901.1, J902.1; also elsewhere on the board
/Power Unit/Camera/V_IN: J902.3; also elsewhere on the board
/Power Unit/GND: J901.2, J902.2, U901.2 (VSS); also elsewhere on the board
/Power Unit/SCL: U901.3 (SCL); also elsewhere on the board
/Power Unit/SDA: U901.4 (SDA); also elsewhere on the board
/Power Unit/VCC: U901.1 (VDD); also elsewhere on the board
unnamed: J904.1, U901.5 (B)
unnamed: J904.2, U901.6 (W)
unnamed: J903.1, Q901.2 (E)
unnamed: J903.2, Q901.3 (C)
unnamed: Q901.1 (B), R901.2

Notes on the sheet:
I^{2}C address W - 0x5C R - 0x5D

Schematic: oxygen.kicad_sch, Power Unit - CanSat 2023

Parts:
C801: 0.1uF; C_0805_2012Metric
C802: 10uF; C_0805_2012Metric
C803: 10nF; C_0805_2012Metric
R801, R802: 100R; R_0805_2012Metric
R803: 20k; R_0805_2012Metric
U801: ME2-02; ME2-O2
U802: MCP6486UT-E/OT; SOT-23-5

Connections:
/Power Unit/GND: C801.2, C802.2, C803.2, R801.2, R802.1, U801.1 (OUT-), U802.2 (V-); also elsewhere on the board
/Power Unit/OXY_{OUT}: C803.1, R803.2, U802.4; also elsewhere on the board
/Power Unit/VCC: C801.1, C802.1, U802.5 (V+); also elsewhere on the board
unnamed: R801.1, U801.2 (OUT), U802.1 (+)
unnamed: R802.2, R803.1, U802.3 (-)



Board: 4 copper layers, 60.7 x 61.3 mm, 102 parts (41 on the bottom side), 70 nets.

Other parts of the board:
kibuzzard-63BEDE70: G***; kibuzzard-63BEDE70
kibuzzard-642731D3: G***; kibuzzard-642731D3
kibuzzard-642753A9: G***; kibuzzard-642753A9
kibuzzard-642757A1: G***; kibuzzard-642757A1
kibuzzard-64275393: G***; kibuzzard-64275393
kibuzzard-64275791: G***; kibuzzard-64275791

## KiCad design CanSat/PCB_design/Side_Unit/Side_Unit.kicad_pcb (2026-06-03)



Board: 2 copper layers, 73.5 x 90.0 mm, 73 parts (14 on the bottom side), 36 nets.

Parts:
C301, C303, C305, C401, C402, C501, C502, C503, C504, C505, C506, C507, C508, C601, C602, C603, C604, C605, C606, C607, C608: 0.1uF; C_0805_2012Metric
C302, C304, C306, C307: 1uF; C_0805_2012Metric
D501, D502, D503, D504, D505, D506, D507, D508, D601, D602, D603, D604, D605, D606, D607, D608: WS2812B; LED_WS2812B_PLCC4_5.0x5.0mm_P3.2mm
J101, J102, J103: Land patern; Land-pattern
R201, R202, R301, R302, R303, R304, R305, R306: 10k; R_0805_2012Metric
U301: AS72651; AMS_LGA-20_4.7x4.5mm_P0.65mm
U302: AS72652; AMS_LGA-20_4.7x4.5mm_P0.65mm
U303: AS72653; AMS_LGA-20_4.7x4.5mm_P0.65mm
U304: AT25SF041B-SSHD-B; SOIC-8_3.9x4.9mm_P1.27mm
U401: BH1730; WSOF6
kibuzzard-63C42A2A: G***; kibuzzard-63C42A2A
kibuzzard-63C42A5F, kibuzzard-63C42A5F#2, kibuzzard-63C42A5F#3: G***; kibuzzard-63C42A5F
kibuzzard-63C42B4A: G***; kibuzzard-63C42B4A
kibuzzard-63C42B39: G***; kibuzzard-63C42B39
kibuzzard-63C86FC3: G***; kibuzzard-63C86FC3
kibuzzard-63C86FCE: G***; kibuzzard-63C86FCE
kibuzzard-63C685CC, kibuzzard-63C685CC#2: G***; kibuzzard-63C685CC
kibuzzard-63C685D8, kibuzzard-63C685D8#2: G***; kibuzzard-63C685D8
kibuzzard-63C6862F: G***; kibuzzard-63C6862F
kibuzzard-63C68642, kibuzzard-63C68642#2: G***; kibuzzard-63C68642
kibuzzard-63C68658: G***; kibuzzard-63C68658

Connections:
/Panel 1/GND: C301.2, C302.2, C303.2, C304.2, C305.2, C306.2, C307.2, C401.1, C402.2, J101.1, U301.16 (GND), U302.16 (GND), U303.16 (GND), U304.4 (GND), U401.2 (INT), U401.3 (GND)
/Panel 1/SCL: J101.2, R202.2, U301.11 (RX/SCL_S), U401.6 (SCL)
/Panel 1/SDA: J101.3, R201.2, U301.12 (TX/SDA_S), U401.4 (SDA)
/Panel 1/Spectroscope Unit/MISO: U301.5 (MISO), U304.2 (SO_(IO1_))
/Panel 1/Spectroscope Unit/MOSI: U301.4 (MOSI), U304.5 (SI_(IO0_))
/Panel 1/Spectroscope Unit/SCK: U301.3 (SCK), U304.6 (SCK)
/Panel 1/Spectroscope Unit/SCL_S: R304.2, U301.9 (SCL_M), U302.9 (SCL_S), U303.9 (SCL_S)
/Panel 1/Spectroscope Unit/SDA_S: R303.2, U301.10 (SDA_M), U302.10 (SDA_S), U303.10 (SDA_S)
/Panel 1/Spectroscope Unit/~CS: U301.6 (~CS), U304.1 (~CS)
/Panel 1/Spectroscope Unit/~RES: R306.2, U301.2 (~RES)
/Panel 1/Spectroscope Unit/~SLV1_RES: R302.2, U301.1 (~SLV1_RES), U302.2 (~RES)
/Panel 1/Spectroscope Unit/~SLV2_RES: R301.2, U301.20 (~SLV2_RES), U303.2 (~RES)
/Panel 1/VCC: C301.1, C302.1, C303.1, C304.1, C305.1, C306.1, C307.1, C401.2, C402.1, J101.4, R201.1, R202.1, R301.1, R302.1, R303.1, R304.1, R305.1, R306.1, U301.14 (VDD2), U301.17 (VDD1), U302.14 (VDD2), U302.17 (VDD1), U303.14 (VDD2), U303.17 (VDD1), U304.3 (~WP_(IO2_)), U304.7 (~HOLD_(IO3_)), U304.8 (VCC), U401.1 (VCC), U401.5 (DVI)
/Panel 2/DIN: D501.4 (DIN), J102.2
/Panel 2/DOUT: D508.2 (DOUT), J102.3
/Panel 2/GND: C501.1, C502.1, C503.1, C504.1, C505.1, C506.1, C507.1, C508.1, D501.3 (VSS), D502.3 (VSS), D503.3 (VSS), D504.3 (VSS), D505.3 (VSS), D506.3 (VSS), D507.3 (VSS), D508.3 (VSS), J102.1
/Panel 2/VCC_5V: C501.2, C502.2, C503.2, C504.2, C505.2, C506.2, C507.2, C508.2, D501.1 (VDD), D502.1 (VDD), D503.1 (VDD), D504.1 (VDD), D505.1 (VDD), D506.1 (VDD), D507.1 (VDD), D508.1 (VDD), J102.4
/Panel 3/DIN: D601.4 (DIN), J103.2
/Panel 3/DOUT: D608.2 (DOUT), J103.3
/Panel 3/GND: C601.1, C602.1, C603.1, C604.1, C605.1, C606.1, C607.1, C608.1, D601.3 (VSS), D602.3 (VSS), D603.3 (VSS), D604.3 (VSS), D605.3 (VSS), D606.3 (VSS), D607.3 (VSS), D608.3 (VSS), J103.1
/Panel 3/VCC_5V: C601.2, C602.2, C603.2, C604.2, C605.2, C606.2, C607.2, C608.2, D601.1 (VDD), D602.1 (VDD), D603.1 (VDD), D604.1 (VDD), D605.1 (VDD), D606.1 (VDD), D607.1 (VDD), D608.1 (VDD), J103.4
unnamed: D501.2 (DOUT), D502.4 (DIN)
unnamed: D502.2 (DOUT), D503.4 (DIN)
unnamed: D503.2 (DOUT), D504.4 (DIN)
unnamed: D504.2 (DOUT), D505.4 (DIN)
unnamed: D505.2 (DOUT), D506.4 (DIN)
unnamed: D506.2 (DOUT), D507.4 (DIN)
unnamed: D507.2 (DOUT), D508.4 (DIN)
unnamed: D601.2 (DOUT), D602.4 (DIN)
unnamed: D602.2 (DOUT), D603.4 (DIN)
unnamed: D603.2 (DOUT), D604.4 (DIN)
unnamed: D604.2 (DOUT), D605.4 (DIN)
unnamed: D605.2 (DOUT), D606.4 (DIN)
unnamed: D606.2 (DOUT), D607.4 (DIN)
unnamed: D607.2 (DOUT), D608.4 (DIN)
unnamed: R305.2, U301.8 (I2C_ENB)

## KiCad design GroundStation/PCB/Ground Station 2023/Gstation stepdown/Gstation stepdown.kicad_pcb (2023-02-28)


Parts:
J1: Input; PinHeader_1x02_P2.54mm_Vertical
J2: Stepdown_SMD; StepDown
J3: Output; PinHeader_1x02_P2.54mm_Vertical

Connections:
unnamed: J1.1, J2.1
unnamed: J1.2, J2.2
unnamed: J2.3, J3.2
unnamed: J2.4, J3.1


Board: 2 copper layers, 33.5 x 18.5 mm, 3 parts (0 on the bottom side), 4 nets.

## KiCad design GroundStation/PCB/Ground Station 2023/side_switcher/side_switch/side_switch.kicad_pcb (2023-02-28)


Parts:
J1, J3: Conn_01x20; PinHeader_1x20_P2.54mm_Vertical
J2: Conn_02x20_Odd_Even; PinHeader_2x20_P2.54mm_Vertical

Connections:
unnamed: J1.2, J2.4
unnamed: J1.3, J2.6
unnamed: J1.5, J2.10
unnamed: J1.9, J2.18
unnamed: J1.10, J2.20
unnamed: J1.11, J2.22
unnamed: J1.12, J2.24
unnamed: J1.13, J2.26
unnamed: J1.14, J2.28
unnamed: J1.15, J2.30
unnamed: J1.20, J2.40
unnamed: J2.1, J3.1
unnamed: J2.3, J3.2
unnamed: J2.21, J3.11
unnamed: J2.25, J3.13
unnamed: J2.27, J3.14

Board: 2 copper layers, 3 parts (0 on the bottom side), 16 nets, no tracks yet.

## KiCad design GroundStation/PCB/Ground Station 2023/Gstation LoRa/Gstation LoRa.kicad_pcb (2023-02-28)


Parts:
AE1: Antenna_Shield; U.FL_Hirose_U.FL-R-SMT-1_Vertical
J1: Conn_02x08_Counter_Clockwise; HOPERF_RFM9XW_SMD
J2: Conn_01x06_Male; PinHeader_1x06_P2.54mm_Vertical
J3: Conn_01x08_Male; PinHeader_1x08_P2.54mm_Vertical

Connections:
unnamed: AE1.1 (A), J1.1
unnamed: AE1.2 (Shield), J1.2
unnamed: J1.3, J2.6
unnamed: J1.4, J2.5
unnamed: J1.5, J2.4
unnamed: J1.6, J2.3
unnamed: J1.7, J2.2
unnamed: J1.8, J2.1
unnamed: J1.9, J3.1
unnamed: J1.10, J3.2
unnamed: J1.11, J3.3
unnamed: J1.12, J3.4
unnamed: J1.13, J3.5
unnamed: J1.14, J3.6
unnamed: J1.15, J3.7
unnamed: J1.16, J3.8



Board: 2 copper layers, 27.0 x 22.0 mm, 4 parts (2 on the bottom side), 16 nets.

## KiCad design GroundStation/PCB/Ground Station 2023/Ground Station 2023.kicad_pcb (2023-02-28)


Board: 2 copper layers, 145.0 x 120.0 mm, 31 parts (0 on the bottom side), 19 nets.

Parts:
ADC1: AD
BME1: BME280
BT1, BT2: Battery_Cell; Battery box
GPS1: GY-NEO6MV2; GPS
LORA1: LORA; Lora deska
RASPI1: Raspberry PI 4B; Raspberry pi 4B
STEPDOWN1: StepDown
SW1: Přepínač; JST_XH_B2B-XH-A_1x02_P2.50mm_Vertical
USB-C1: USB-C; JST_XH_B2B-XH-A_1x02_P2.50mm_Vertical
kibuzzard-63C06CDD: G***; kibuzzard-63C06CDD
kibuzzard-63C07A1A: G***; kibuzzard-63C07A1A
kibuzzard-63C07A12: G***; kibuzzard-63C07A12
kibuzzard-63C07ADB: G***; kibuzzard-63C07ADB
kibuzzard-63C07B39: G***; kibuzzard-63C07B39
kibuzzard-63C07B83: G***; kibuzzard-63C07B83
kibuzzard-63C07C6F: G***; kibuzzard-63C07C6F
kibuzzard-63C07C98: G***; kibuzzard-63C07C98
kibuzzard-63C07CF0: G***; kibuzzard-63C07CF0
kibuzzard-63C07D65: G***; kibuzzard-63C07D65
kibuzzard-63C07E6F: G***; kibuzzard-63C07E6F
kibuzzard-63C07E43: G***; kibuzzard-63C07E43
kibuzzard-63C070CF: G***; kibuzzard-63C070CF
kibuzzard-63C071A1: G***; kibuzzard-63C071A1
kibuzzard-63C072BC: G***; kibuzzard-63C072BC
kibuzzard-63C074B7, kibuzzard-63C074B7#2: G***; kibuzzard-63C074B7
kibuzzard-63C0733F: G***; kibuzzard-63C0733F
kibuzzard-63C0781A: G***; kibuzzard-63C0781A
kibuzzard-63C0785A: G***; kibuzzard-63C0785A
kibuzzard-63C07127: G***; kibuzzard-63C07127

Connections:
+3V3: BME1.4, LORA1.5, RASPI1.1, RASPI1.17
+5V: ADC1.10, GPS1.1, RASPI1.2, RASPI1.4
DI00: LORA1.6, RASPI1.29
GNDD: ADC1.6, ADC1.9, BME1.3, GPS1.4, LORA1.9, LORA1.16, RASPI1.6, RASPI1.9, RASPI1.14, RASPI1.20, RASPI1.25, RASPI1.30, RASPI1.34, RASPI1.39
IN+: BT1.1 (+), STEPDOWN1.2 (Pin_7)
IN-: STEPDOWN1.1, SW1.2 (B)
MISO: LORA1.10, RASPI1.21
MOSI: LORA1.11, RASPI1.19
NSS: LORA1.13, RASPI1.26
unnamed: ADC1.4, BT1.2 (-), BT2.1 (+)
unnamed: BT2.2 (-), SW1.1 (A)
OUT+: STEPDOWN1.4 (Pin_6), USB-C1.2
OUT-: STEPDOWN1.3 (Pin_2), USB-C1.1
RESET: LORA1.14, RASPI1.22
RXD2: GPS1.3, RASPI1.28
SCK: LORA1.12, RASPI1.23
SCL: ADC1.8, BME1.2, RASPI1.5
SDA: ADC1.7, BME1.1, RASPI1.3
TXD2: GPS1.2, RASPI1.27

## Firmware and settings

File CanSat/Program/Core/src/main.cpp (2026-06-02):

//TODO camPower IRQ časovač
//TODO animace LED
//TODO findMe svit
//fTODO po každém uložení ukončit SD kartu (zkusit)
//dTODO zkalibrovat kyslík - done

//17:56 - 7.74V

#include "globalVars.h"

#include "RTOS_tasks.h"
#include "esp32/rom/rtc.h"
#include <esp_task_wdt.h>

#include "myTime.h"
#include "temperature.h"
#include "gps.h"
#include "myLora.h"
#include "myINA.h"
#include "mySD.h"
#include "myServer.h"
#include "myOxygen.h"
#include "myNeo.h"
#include "myINA.h"
#include "myCO2.h"
#include "myBNO.h"
#include "myBH1730.h"
#include "mySpectro.h"
#include "pot.h"
#include "gpioExtender.h"
#include "camera.h"

bool doDebug;
String serialBuffer;
bool softwareReset;
bool launched;

MyBme bme(0x77);
MyGPS gps(0x42);
MyLora lora(&SPI, 433E6, 32, 13, 39, 0xFF, 17);
MyINA ina(0x45);
MySD sd(26);
File myFile;
MyServer server(80);
MyWiFi wifi("Project-SkyFall", "1234abcd");
MyTime rtc(0x68);
MyOxygen oxygen(36);
MyDS18B20 ds18(&oneWire, 4);
MyNeo neo(16, 10, 23, NEO_GRB + NEO_KHZ800);
#define DOPLNIT 0
MyIMU bno(30, 0x28, DOPLNIT); //TODO doplnit
MyCO2 scd(0x62);
MyBH1730 bh(BH1730_GAIN::GAIN_X1);
MySpectro asx;
Pot pot(0x2E);
PCA8574 pca(0x20);
Camera cam;

TaskHandle_t runServer_handle;
TaskHandle_t printData_hadle;
TaskHandle_t saveData_handle;
TaskHandle_t openFile_handle;
TaskHandle_t getData_handle;
TaskHandle_t runNeo_handle;
TaskHandle_t isrHandleDioRise_handle;
TaskHandle_t loraCheckTxDone_handle;
TaskHandle_t ds18getData_handle;
TaskHandle_t gpsGetData_handle;
//TaskHandle_t measureBattery_handle;

TickType_t getData_lastTime;
TickType_t refreshRate = 1000;

SemaphoreHandle_t spiSemaphore_hadle = NULL;
SemaphoreHandle_t gpsGetDataDone_semaphore = NULL;
SemaphoreHandle_t ds18GetDataDone_semaphore = NULL;
SemaphoreHandle_t saveData_semaphore = NULL;
SemaphoreHandle_t openFile_semaphore = NULL;

OneWire oneWire;

void setup(void) {
  Serial.begin(115200);
  Serial1.begin(4800, SERIAL_8N2, SM_A_PIN, DUMMY_PIN);
  Wire.begin(21, 22, 400000ul);
  Wire1.begin(19, 18, 100000ul);
  oneWire.begin(4);
  SPI.begin(33, 27, 14);
  SPI.setFrequency(20000000);
  
  pinMode(lora.cs, OUTPUT); digitalWrite(lora.cs, HIGH);
  pinMode(sd.cs, OUTPUT); digitalWrite(sd.cs, HIGH);

  pinMode(RUN_SEVER_PIN, INPUT);
  pinMode(37, INPUT);

  Serial.println("Core 0 restart reason: " + verbose_print_reset_reason(rtc_get_reset_reason(0)));
  Serial.println("Core 1 restart reason: " + verbose_print_reset_reason(rtc_get_reset_reason(1)));

  if(rtc_get_reset_reason(0) == 12){
    Serial.println("Watchdog reset");
    sd.mode = Mode::mode_SLEEP;
    softwareReset = true;
  }

  spiSemaphore_hadle = xSemaphoreCreateBinary();
  ds18GetDataDone_semaphore = xSemaphoreCreateBinary();

  xSemaphoreGive(spiSemaphore_hadle);

  Serial.println('\n');
  printResult(pca.setup(true));
  printResult(cam.setup(true));
  printResult(rtc.setup(true));
  printResult(sd.setup(true));
  printResult(gps.setup(true));
  printResult(bme.setup(true));
  printResult(ds18.setup(true));
  printResult(lora.setup(true));
  printResult(ina.setup(true));
  printResult(oxygen.setup(true));
  printResult(neo.setup(true));
  printResult(scd.setup(true));
  printResult(bno.setup(true));
  printResult(bh.setup(true));
  printResult(asx.setup(true));
  printResult(pot.setup(true));

  xTaskCreate(runServer, "Run Server", 4096, NULL, 3, &runServer_handle);
  xTaskCreate(runNeo, "Run Neo Pixels", 2048, NULL, 3, &runNeo_handle);

  xTaskCreate(printData, "Print Data", 4096, NULL, 5, &printData_hadle);
  xTaskCreate(openFile, "Open SD file", 4096, NULL, 6, &openFile_handle);

  xTaskCreate(isrHandleDioRise, "ISR DIO Rise", 2048, NULL, 15, &isrHandleDioRise_handle);

  xTaskCreate(ds18getData, "DS18B20 get data", 2048, NULL, 5, &ds18getData_handle);
  xTaskCreate(gpsGetData, "GPS get data", 4096, NULL, 5, &gpsGetData_handle);
  xTaskCreate(getData, "Get Data Task", 4096, NULL, 7, &getData_handle);

  xTaskCreate(controlTask, "Control Task", 8192, NULL, 1, NULL);
}

void loop(void) {
}

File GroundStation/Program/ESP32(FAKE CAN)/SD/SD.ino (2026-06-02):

/*
  Rui Santos
  Complete project details at https://RandomNerdTutorials.com/esp32-microsd-card-arduino/

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
  The above copyright notice and this permission notice shall be included in all
  copies or substantial portions of the Software.
*/

// Libraries for SD card
#include "FS.h"
#include "SD.h"
#include "SPI.h"

SPIClass spi = SPIClass(VSPI);

#define SCK  18
#define MISO  19
#define MOSI  23
#define CS  17

String lines[200];
int n = 0;
char dataread[200];
int l = 0;
int j = 0;
bool openable;





void setup() {
  Serial.begin(115200);

  spi.begin(SCK, MISO, MOSI, CS);

  initSDCard();

  // If the data.txt file doesn't exist
  // Create a file on the SD card and write the data labels
  File file = SD.open("/data.txt");
  if (!file) {
    Serial.println("File doesn't exist");
    Serial.println("Creating file...");
    writeFile(SD, "/data.txt", "Test File --- Lets GO \r\n");
  }
  else {
    Serial.println("File already exists");
  }
  file.close();

}

void loop() {
  delay(500);
  readFile(SD, "/test.txt");


  //Serial.print(dataread);
  if (openable == true) {
    if (dataread[l] != (42)) {
      while (dataread[l] != (13)) {
        lines[j] += dataread[l];
        l++;
      }
      lines[j] += ("\r\n");
      j++;
      l++;
    }
    if (dataread[l] == (42)) {
      l = 0;
      j = 0;
    }
  }
  Serial.print(lines[0]);
  Serial.print(lines[1]);
  Serial.print(lines[2]);
  Serial.print(lines[3]);
  Serial.print(lines[4]);



  Serial.print("\r\n");




}

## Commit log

2022-12-22 Initial push
    [CanSat 2023 - Elektrokonstrukce-B_Cu.gbr, CanSat 2023 - Elektrokonstrukce-B_Fab.gbr, CanSat 2023 - Elektrokonstrukce-B_Mask.gbr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]
2022-12-26 Placed capacitor, no DRC errors
    [Control Unit.kicad_pcb, Control Unit.kicad_sch]
2022-12-26 Renumbered Control Unit sheets
    [batteryCharger.kicad_sch, batteryPack.kicad_sch, bme280.kicad_sch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]
2022-12-26 Changed packages 0402 -> 0804
    [Control Unit.kicad_pcb, Control Unit.kicad_sch, bme280.kicad_sch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]
2022-12-27 Fixed clipped silkscreen
    [Control Unit.kicad_pcb, Control Unit.kicad_sch]
2022-12-27 Renumbered references - power unit
    [Power Unit.kicad_pcb, Power Unit.kicad_sch, bme280.kicad_sch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]
2022-12-27 Changed RX, TX leds
    [Control Unit.kicad_pcb, Control Unit.kicad_sch, controlUnit.kicad_sch]
2022-12-29 Changed order of pins - J2
    [Control Unit.kicad_pcb, Control Unit.kicad_sch, bme280.kicad_sch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]
2023-01-03 Complete layout - zero error - Power Unit
    [Power Unit.kicad_pcb, batteryPack.kicad_sch, camera.kicad_sch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]
2023-01-03 Added 3D models folder
    [SEN0322_Gravity_Oxygen.stp]
2023-01-06 Edge cuts v0.1
    [Control Unit-B_Fab.dxf, Control Unit-Edge_Cuts.dxf]
2023-01-06 Side Units - blank project
    [Side Unit.kicad_pcb, Side Unit.kicad_sch]
2023-01-06 Create Control Unit-Edge_Cuts_Edited.dxf
    [Control Unit-Edge_Cuts_Edited.dxf]
2023-01-07 Update Control Unit-Edge_Cuts_Edited.dxf
    [Control Unit-Edge_Cuts_Edited.dxf]
2023-01-07 add edge_cuts_DXFs
    [Power Unit-Edge_Cuts_Edited.dxf]
2023-01-07 WIP commit
    [Control Unit.kicad_pcb, Control Unit.kicad_sch, Power Unit-Edge_Cuts.dxf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]
2023-01-07 trying to fix fucking kiCad
    [Control Unit-Edge_Cuts_Edited.dxf, Power Unit-Edge_Cuts_Edited.dxf]
2023-01-07 fuck your mum kicad
    [Control Unit-Edge_Cuts_Edited.dxf, Power Unit-Edge_Cuts_Edited.dxf]
2023-01-07 kicad fock you last time
    [Control Unit-Edge_Cuts_Edited.dxf, Power Unit-Edge_Cuts_Edited.dxf]
2023-01-07 New edge cuts
    [Control Unit.kicad_pcb]
2023-01-10 changed PCBs DXFs
    [Control Unit-Edge_Cuts_Edited.dxf, Power Unit-Edge_Cuts_Edited.dxf]
2023-01-10 Create 62mm_diameter + threaded rod.dxf
    [62mm_diameter + threaded rod.dxf]
2023-01-12 Create Side PCBs dimensionss.dxf
    [Side PCBs dimensionss.dxf]
2023-01-12 Create Control Unit-Edge_Cuts_Edited_threaded.dxf
    [Control Unit-Edge_Cuts_Edited_threaded.dxf]
2023-01-12 DXF logo
    [Logo_vFINAL.dxf]
2023-01-12 final final edge cuts
    [Control Unit-Edge_Cuts_Edited.dxf, Control Unit-Edge_Cuts_Edited_threaded.dxf, Power Unit-Edge_Cuts_Edited_threaded.dxf]
2023-01-12 PCB FINAL?
    [Ground Station 2023.kicad_pcb]
2023-01-15 Modified Logo_vFINAL.dxf
    [Logo_vFINAL.dxf]
2023-01-15 Updated 3D exports
    [Side Unit.step]
2023-01-17 Production folder
    [bom.csv, designators.csv, positions.csv]
2023-01-17 Production files
    [bom.csv, designators.csv, positions.csv]
2023-01-17 Updated gitignore (removed Side Unit-backup, *.kicad_prl
2023-01-17 LoRa step
    [RFM95 LoRa v15.stp]
2023-01-17 Working version of PCBs (before final)
    [Control Unit.kicad_sch, Power Unit.kicad_sch, Side Unit.kicad_pcb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]
2023-01-17 3D export
    [Side Unit.step]
2023-01-17 PCB before last check
    [Side Unit.kicad_pcb, designators.csv, positions.csv]
2023-01-17 Added component values
    [batteryCharger.kicad_sch]
2023-01-17 Realignmented Pinheaders
    [Power Unit.kicad_sch, bom.csv, positions.csv]
2023-01-17 Create ESP32PICOMINI02 v14.step
2023-01-18 18.1.2023 - final
    [BOM.xlsx, Control Unit.kicad_sch, Power Unit.kicad_sch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]
2023-01-19 Add LoRa breakup board
    [Gstation LoRa.kicad_pcb, Gstation LoRa.kicad_sch]
2023-01-21 PCB FINAL snad
    [Ground Station 2023.kicad_pcb, Gstation stepdown.kicad_pcb, designators.csv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]
2023-01-24 Final PCBs 24.1.2023
    [Ground Station 2023.kicad_pcb, Gstation LoRa.kicad_pcb, Gstation LoRa.step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]
2023-01-30 Added DS18B20 sensor
2023-02-07 Optimized verbose print options
2023-02-07 Added fiducial markers
    [Side Unit.kicad_pcb, designators.csv]
2023-02-07 Renumbered parts
    [BOM.xlsx, Control Unit.kicad_sch, bom.csv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]
2023-02-07 Renewed folder path
    [62mm_diameter + threaded rod.dxf, BOM.xlsx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]
2023-02-10 Fixed SPI CS syntax error - removed unused object
    [main.cpp]
2023-02-16 Created MyLora::dumpRegisters -modified former dumpRegisters to print in binary
2023-02-18 SD repeatable mount + SDcard tries to mount 5 times before aborting
2023-02-18 Server and Wifi + added default FALSE verbose option in `server.setup()` + created MyWiFi constructor + `softAP()` now takes privated variables + low TX power -> 20dBm + `MyServer::mode()` + `MyServe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
2023-02-18 Created myTask resume + tries to resume task in try{} block (hopefully will resolve crashes)
    [RTOS_tasks.cpp]
2023-02-25 PrintResult print style ~ changed - for =
2023-03-22 Main update
    [Ground Station 2023.kicad_sch]
2023-03-25 Fixed SCD41 returned fail in setup
    [myCO2.cpp]
2023-03-25 Task notify system + GPS get data notify + DS18 get data notify [fix needed]
    [RTOS_tasks.cpp]
2023-04-26 current plot
2023-04-26 camera update
2023-06-21 SD card rework ~Files now dont close¨ ~No crashes -Unused tasks
    [RTOS_tasks.cpp, main.cpp]
2026-06-02 Ground station (#22)
    * asddada
    * dasd
    * Main update
    * Fungující GS(verze v den finále v 4:45)
    * adata
    ---------
2026-06-02 Visualization (#23)
    * Debug
    * Untest
    * Window resize
    * Trajectory
    * Untest
    * Delete test data
    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
2026-06-03 Cleanup (#26)
    * First commit
    * Modifying README.md
    * Složka vytvořena
    * Zkouška sirén
    * Spraveno
    * Update README.md
    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
    [122-2312-GR.SchLib, 122-2312-GR.stp, 1222312GR.PcbLib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]
